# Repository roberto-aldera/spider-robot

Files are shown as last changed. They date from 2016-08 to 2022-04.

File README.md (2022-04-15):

# spider-robot 🕷️
⚠️ Messy research code 👨‍🎓

This repo contains the source code from my undergraduate mechatronics thesis project at the University of Cape Town.
An STM iNEMO was used for the data logging and control of a bio-inspired spider robot.
The majority of the development code is in C for use onboard the microcontroller, with some C# that was required for a logging app on my laptop.

📽️ Demo video available [here](https://youtu.be/Y-Pgbu4grWk).

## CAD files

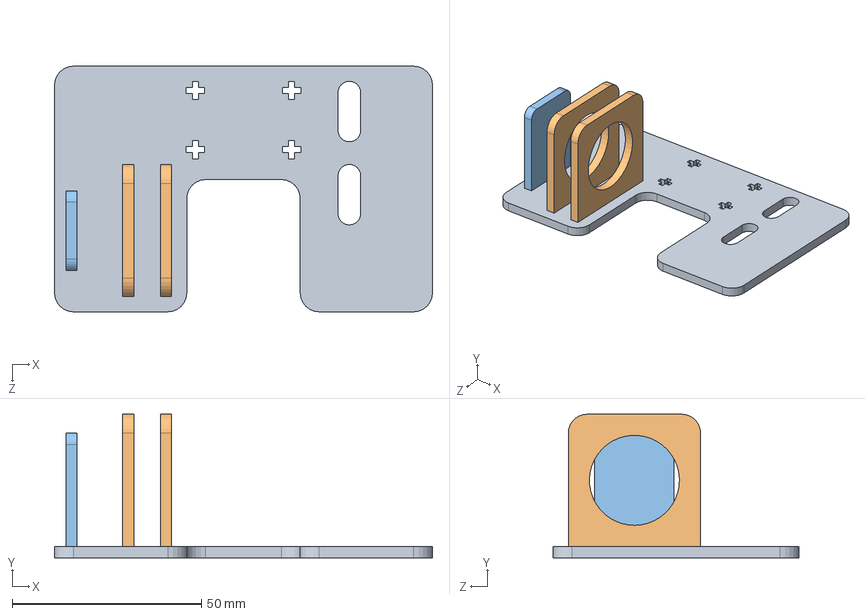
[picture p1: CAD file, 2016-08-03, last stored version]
SolidWorks parts/base_plate_assembly.SLDASM
100.0 x 38.0 x 65.0 mm
base_plate
dragline_motor_arch x 2
encoder_mount

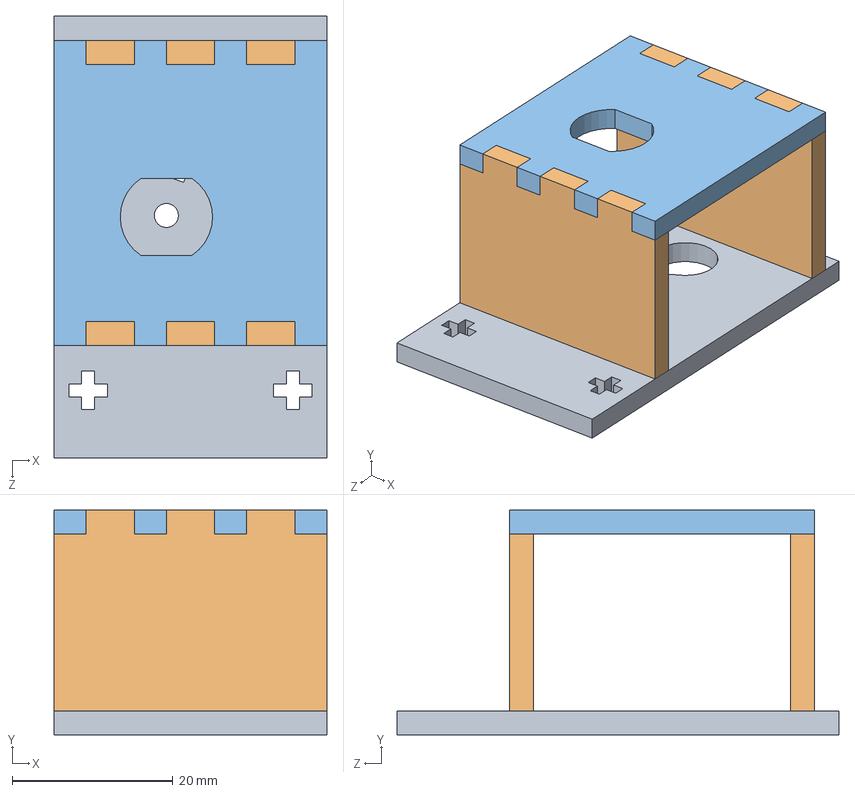
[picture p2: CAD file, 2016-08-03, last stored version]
SolidWorks parts/nail_launcher.SLDASM
34.0 x 28.0 x 55.0 mm
launcher_slot_new
launcher_motor_sides x 2
launcher_motor_holder

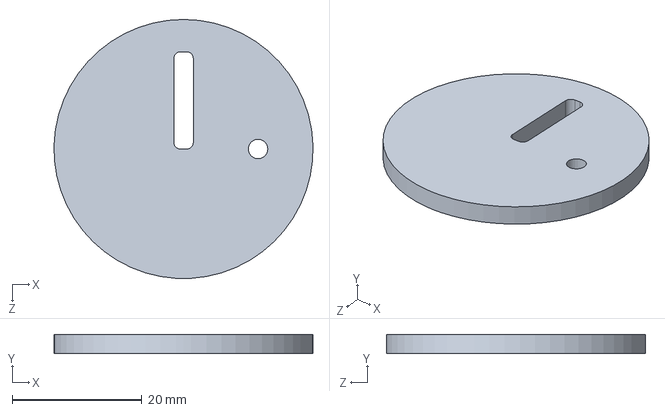
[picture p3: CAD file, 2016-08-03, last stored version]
SolidWorks parts/launcher_disc_slot.SLDPRT
40.0 x 3.00 x 40.0 mm

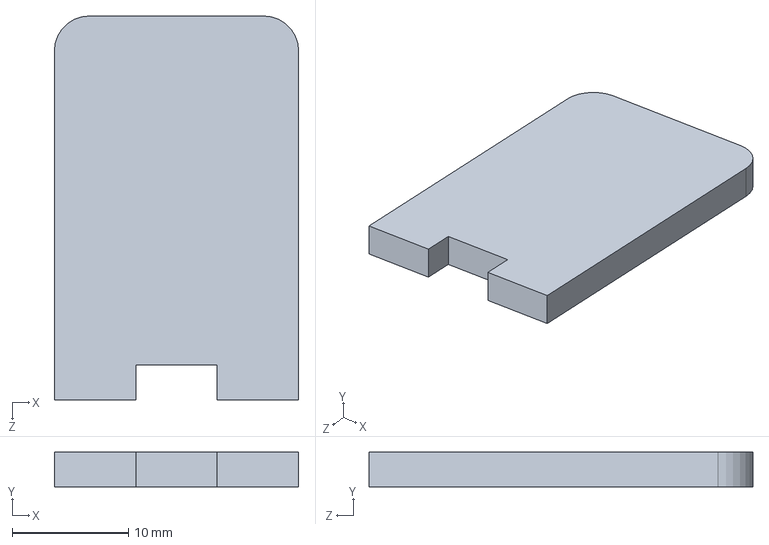
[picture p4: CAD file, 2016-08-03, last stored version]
SolidWorks parts/encoder_mount.SLDPRT
21.0 x 3.00 x 33.0 mm

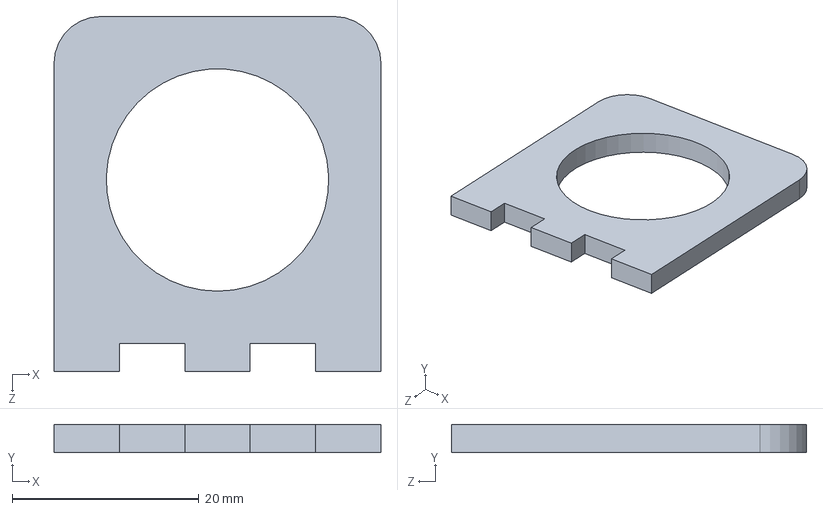
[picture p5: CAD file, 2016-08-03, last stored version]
SolidWorks parts/dragline_motor_arch.SLDPRT
35.0 x 3.00 x 38.0 mm

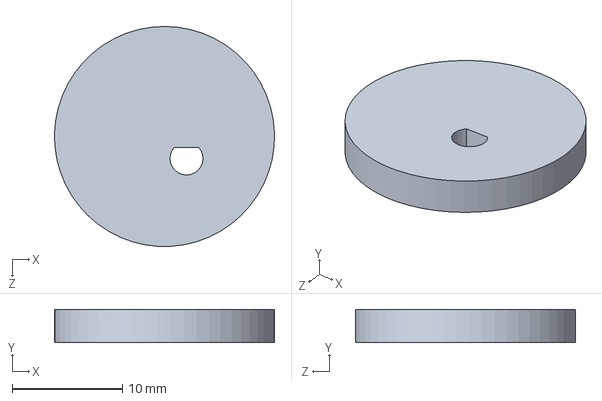
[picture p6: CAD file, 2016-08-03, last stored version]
SolidWorks parts/launcher_simple_cam.SLDPRT
20.0 x 3.00 x 20.0 mm

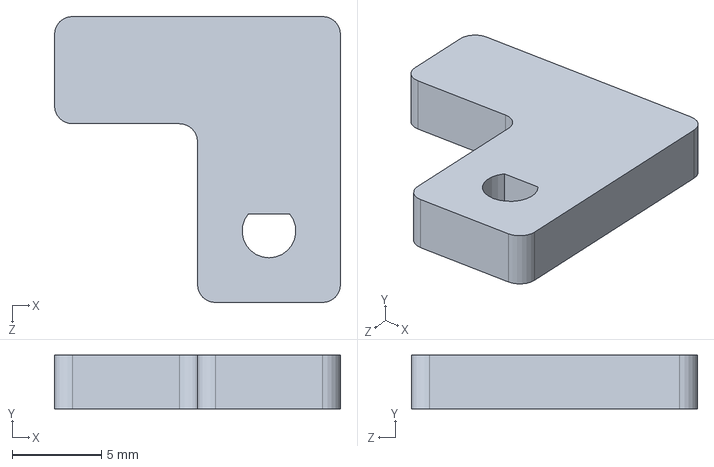
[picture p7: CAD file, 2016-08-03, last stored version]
SolidWorks parts/launcher_motor_L_arm.SLDPRT
16.0 x 3.00 x 16.0 mm

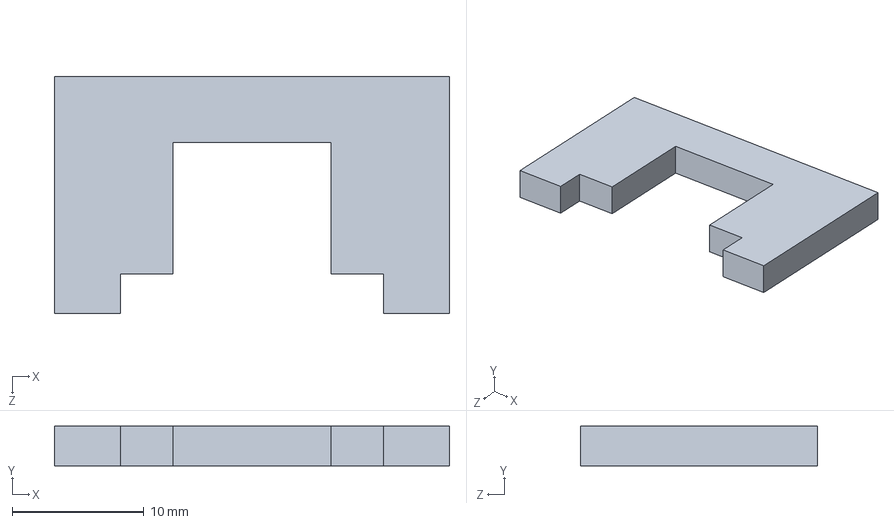
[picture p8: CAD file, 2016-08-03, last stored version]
SolidWorks parts/launcher_motor_arch.SLDPRT
30.0 x 3.00 x 18.0 mm

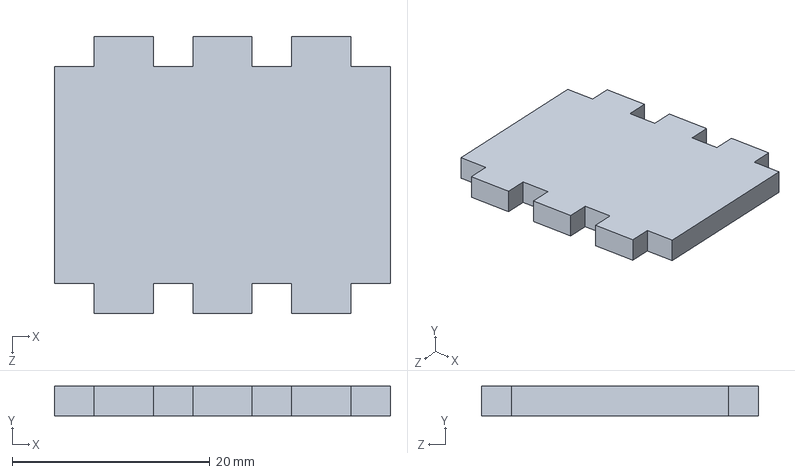
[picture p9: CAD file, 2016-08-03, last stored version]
SolidWorks parts/launcher_motor_sides.SLDPRT
34.0 x 3.00 x 28.0 mm

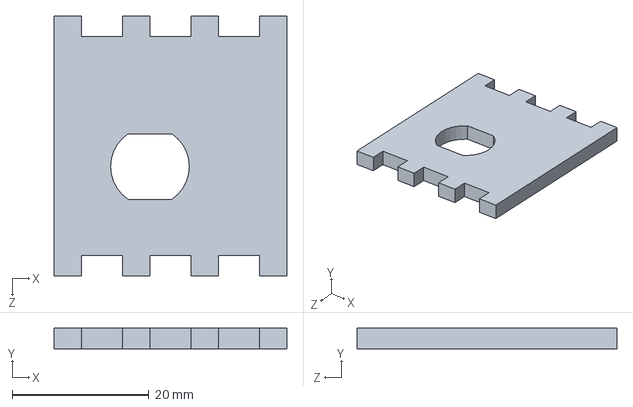
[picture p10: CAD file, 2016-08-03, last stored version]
SolidWorks parts/launcher_motor_holder.SLDPRT
34.0 x 3.00 x 38.0 mm

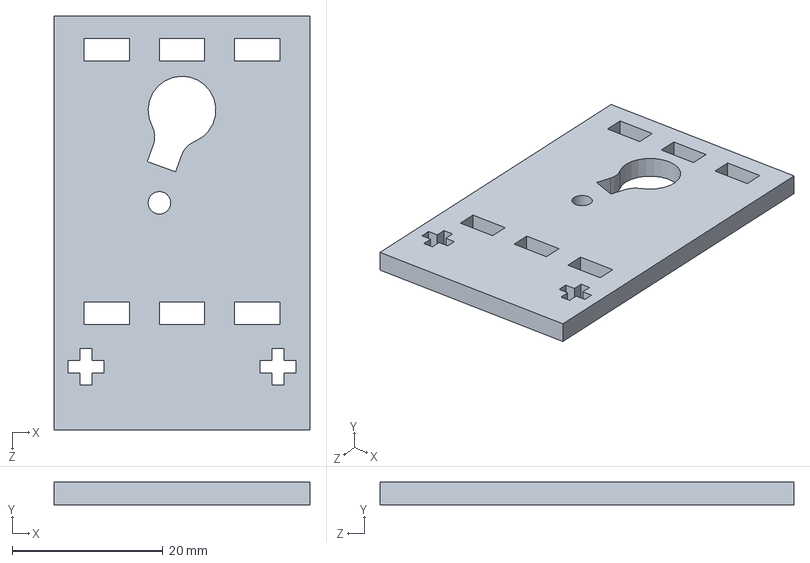
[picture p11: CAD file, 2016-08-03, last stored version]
SolidWorks parts/launcher_slot_new.SLDPRT
34.0 x 3.00 x 55.0 mm

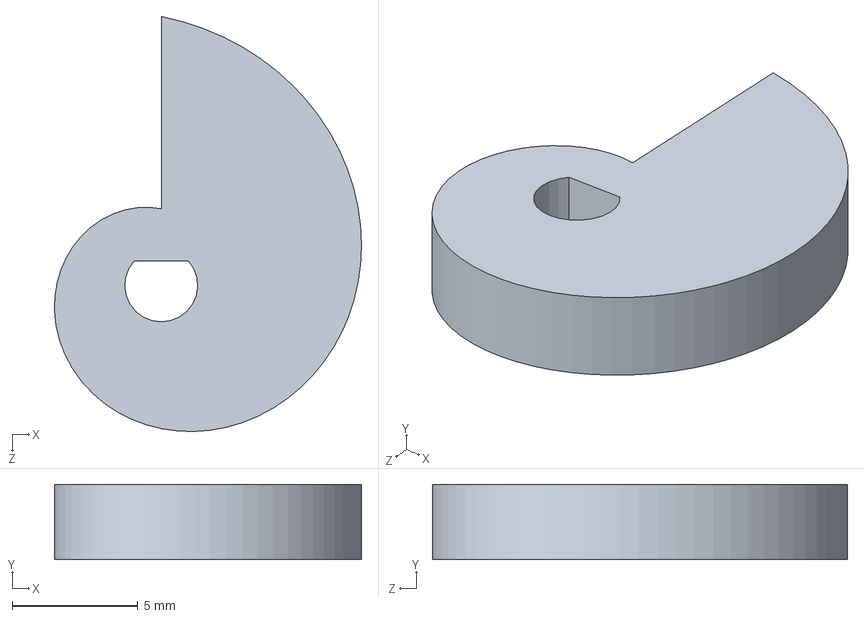
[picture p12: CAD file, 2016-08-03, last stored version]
SolidWorks parts/Nautilus_cam.SLDPRT
12.2 x 3.00 x 16.5 mm

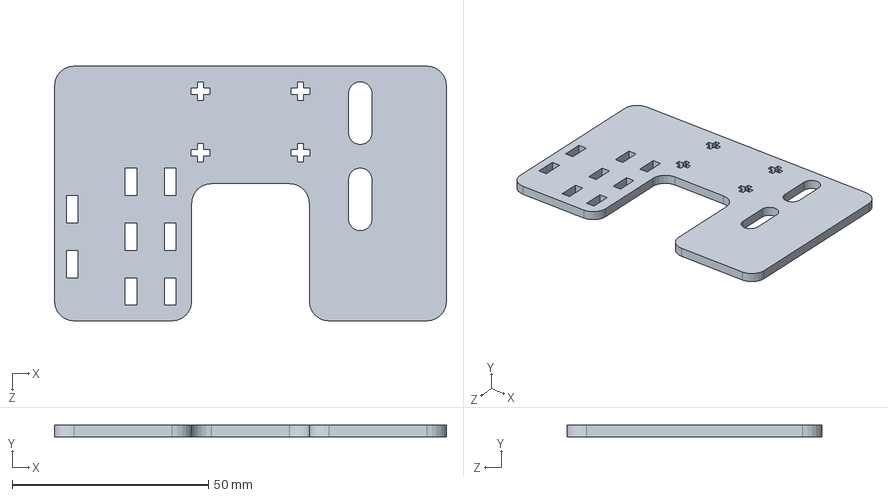
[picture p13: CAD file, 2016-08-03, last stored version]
SolidWorks parts/base_plate.SLDPRT
100.0 x 3.00 x 65.0 mm

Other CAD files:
SolidWorks parts/Nautilus_cams_sizing.SLDDRW
SolidWorks parts/base_plate_iterations.SLDDRW
SolidWorks parts/launcher_iterations.SLDDRW

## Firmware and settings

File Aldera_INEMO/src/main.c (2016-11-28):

/*
 * main.c
 *
 *  Created on: May 25, 2014
 *  Original author: Callen Fisher
 *  Current author: Roberto Aldera, Thesis 2016
 */
//Include all the relevant (header) files
//#include <stddef.h>
#include "stm32f10x.h"
#include "AccMag.h"
#include "controlLoopTimer.h"
#include "gpioPorts.h"
#include "gyro.h"
#include "testPorts.h"
#include "XBEE.h"
#include "USART.h"
#include "DMA.h"
#include "ADC.h"
#include "control.h"
#include "send.h"
#include "serial_terminal.h"
#include "CRC.h"
#include "pwm.h"

uint8_t acc8[6];		//3 axes, each returning uint16_t, 3x2=6
uint8_t mag8[6];
uint8_t gyro8[6];
uint8_t angles8[12];
uint8_t MiscPayload8[17];	//temperature=1 (just ADCtemp),PWM=4,Encoder=4+4, currentSensor=4
uint16_t encoderPosition = 0;
uint16_t adcValDMA[2];	//to store temperature and current sensor readings
uint16_t testVar[2];	//debugging purposes
uint8_t temperature[2];
uint8_t status = 0;
uint8_t XBee_waiting = 0;
uint8_t activateControl = 0;
float acc[3];
float accCalib[3];
float mag[3];
float gyro[3];
float gyroCalib[3];
float angles[3];
float velocities[3];
float positions[3];
float PWMval;
float shaft_revs = 0;
float shaft_speed = 0;
float motorCurrent;	//ADC reading from motor current sensor

void setUpEncoder();
void convertDataToBytes(void);
void toggleGPIOpin(uint8_t *status);

uint8_t a8[] = { 65, 66, 67, 68, 69, 70 };	//debugging
uint8_t b8[] = { 106, 107, 108, 109, 110, 111 };	//debugging
uint8_t c8[] = { 74, 75, 76, 77, 78, 79, 74, 75, 76, 77, 78, 79 };	//debugging
uint8_t d8[] = { 97, 98, 99, 100, 101, 102, 103, 102, 101, 100, 99, 98, 97 };//debugging

int main(void) {
	serialTerminal_Init();
	setUpLoopTimer();
	setUpEncoder();
	setUpGPIO();
	setUpEcompass();
	setUpGyro();
	setUpADC();	//this also sets up DMA...
	//setUpXbee(); //unused, replaced with SD card logging
	setUpLoggerSDcard();
	setUpPWM();

//	for(int i = 0; i < 999999; i++){
//	//ensure the data.txt file starts with the beginning of a packet
//	}

	while (1) {
		toggleGPIOpin(&status);
		getAcc(acc8, acc);		//this takes long
		getGyro(gyro8, gyro);
		//		getMag(mag8, mag);
		//		getTempCelsius(temperature);
		readADCdma(adcValDMA,&motorCurrent);	//for getting temperature, a u16 val
		//readADC_motorCurrent(&motorCurrent);	//for getting current, a float val
		temperature[1] = (uint8_t)((V25 - adcValDMA[0]) / Avg_Slope + 25);
		readEncoder(&shaft_revs, &shaft_speed);
		calibrateMEMS(acc, accCalib, gyro, gyroCalib, temperature);
		controlMethod(accCalib, gyroCalib, temperature, angles, velocities, positions,
				&PWMval, &shaft_revs, &activateControl);

		for (int p = 0; p < sizeof(TxBuff); p++) {
			TxBuff[p] = 0;
		}

		DMA_Cmd(DMA1_Channel7, DISABLE);
		DMA_SetCurrDataCounter(DMA1_Channel7, sizeof(TxBuff));
		DMA_Cmd(DMA1_Channel4, DISABLE);
		DMA_SetCurrDataCounter(DMA1_Channel4, sizeof(TxBuff));

		//Four payloads, gyro/acc/angles/MiscPayload
		convertDataToBytes();
		serialTerminal_packetize(gyro8, acc8, angles8, MiscPayload8,
				sizeof(gyro8), sizeof(acc8), sizeof(angles8),
				sizeof(MiscPayload8));

		//debugging purposes
		//		serialTerminal_packetize(a8, b8, c8, d8, sizeof(a8), sizeof(b8),
		//				sizeof(c8), sizeof(d8));

		//SD card data
		DMA_Cmd(DMA1_Channel4, ENABLE);
		USART_DMACmd(USART1, USART_DMAReq_Tx, ENABLE);
		USART_Cmd(USART1, ENABLE);

		//XBee data, slower
//		if (XBee_waiting == 10) {
//			DMA_Cmd(DMA1_Channel7, ENABLE);
//			USART_DMACmd(USART2, USART_DMAReq_Tx, ENABLE);
//			USART_Cmd(USART2, ENABLE);
//			XBee_waiting = 0;
//		}
//		XBee_waiting++;
		//Toggle PA11 to test loop frequency
		toggleGPIOpin(&status);
		//wait until next run, to maintain 200Hz sync
		waitForEndTimerHz();
	}
}

void toggleGPIOpin(uint8_t *status) {
	if (*status == 0) {
		GPIO_SetBits(GPIOA, GPIO_Pin_11);
		*status = 1;
	} else {
		GPIO_ResetBits(GPIOA, GPIO_Pin_11);
		*status = 0;
	}
}

void convertDataToBytes() {
	union {
		char temp_char[12];
		float temp_int_buffer[3];
	} buffer_to_char_union1;
	buffer_to_char_union1.temp_int_buffer[0] = angles[0];
	buffer_to_char_union1.temp_int_buffer[1] = angles[1];
	buffer_to_char_union1.temp_int_buffer[2] = angles[2];
	for (int i = 0; i < 12; i++) {
		angles8[i] = buffer_to_char_union1.temp_char[i];
	}

	//	union {
	//		uint8_t temp_signed[2];
	//		uint8_t temp_unsigned[2];
	//	} buffer_to_char_union2;
	//	//temperatureToPack[1] = 30;
	//	buffer_to_char_union2.temp_signed[0] = temperature[0];
	//	buffer_to_char_union2.temp_signed[1] = temperature[1];
	//	for (int i = 0; i < 2; i++) {
	//		MiscPayload8[i] = buffer_to_char_union2.temp_unsigned[i];
	//	}
	for (int i = 0; i < 1; i++) {
		//		MiscPayload8[i] = temperature[i];
		MiscPayload8[0] = temperature[1];
	}

	union {
		char temp_char[4];
		float temp_int_buffer;
	} buffer_to_char_union3;
	buffer_to_char_union3.temp_int_buffer = PWMval;
	for (int i = 1; i < 5; i++) {
		MiscPayload8[i] = buffer_to_char_union3.temp_char[i - 1];
	}

	union {
		char temp_char[4];
		float temp_int_buffer;
	} buffer_to_char_union4;
	buffer_to_char_union4.temp_int_buffer = shaft_revs;
	for (int i = 5; i < 9; i++) {
		MiscPayload8[i] = buffer_to_char_union4.temp_char[i - 5];
	}

	union {
		char temp_char[4];
		float temp_int_buffer;
	} buffer_to_char_union5;
	buffer_to_char_union5.temp_int_buffer = shaft_speed;
	for (int i = 9; i < 13; i++) {
		MiscPayload8[i] = buffer_to_char_union5.temp_char[i - 9];
	}

	union {
		char temp_char[4];
		float temp_int_buffer;
	} buffer_to_char_union6;
	buffer_to_char_union6.temp_int_buffer = motorCurrent;
	for (int i = 13; i < 17; i++) {
		MiscPayload8[i] = buffer_to_char_union6.temp_char[i - 13];
	}
}

///////////////////////////////////////////////////////////////////////////
/////don't delete the following functions//////////////////////////////////
///////////////////////////////////////////////////////////////////////////
void __assert_func(const char *file, int line, const char *func,
		const char *failedexpr) {
	while (1) {
	}
}
void __assert(const char *file, int line, const char *failedexpr) {
	__assert_func(file, line, NULL, failedexpr);
}

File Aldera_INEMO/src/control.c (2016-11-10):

/*
 * control.c
 *
 *  Created on: Jun 9, 2014
 *  Template: Callen Fisher
 *  Author: Roberto Aldera
 *
 */

#include "control.h"

void readEncoder(float *shaft_revs, float *shaft_speed) {

	static volatile int16_t oldShaftEncoder;
	static volatile int16_t shaftEncoder;
	static float position = 0;

	oldShaftEncoder = shaftEncoder;
	shaftEncoder = TIM_GetCounter(TIM3);
	*shaft_speed = shaftEncoder - oldShaftEncoder;
	position += *shaft_speed;
	*shaft_revs = position;
	//	if (shaftEncoder > 32768) {
	//		shaftEncoder = -(65536 - shaftEncoder);
	//	}
	//	*shaft_revs = (position) ;//(1/(3*2));	//3 teeth on encoder wheel
	//*shaft_speed = *shaft_speed / 0.01;

}

void calibrateMEMS(float* acc, float* accCalib, float* gyro, float* gyroCalib, u8* temperature){
	accCalib[0] = 0.9922*acc[0] - 0.0247*acc[1] + 0.0225*acc[2] + 0.0468;
	accCalib[1] = 0.0453*acc[0] + 0.9574*acc[1] + 0.0072*acc[2] + 0.022;
	accCalib[2] = -0.0141*acc[0] -0.0037*acc[1] + 0.9971*acc[2] + 0.0053;

	gyroCalib[0] = gyro[0] + (0.060394*temperature[1] - 3.0843);
	gyroCalib[1] = gyro[1] + (0.025522*temperature[1] - 0.40084);
	gyroCalib[2] = gyro[2] + (-0.32248*temperature[1] + 11.3496);
}

void controlMethod(float*accCalib, float*gyroCalib, uint8_t*temp, float*angles, float*velocities,
		float*positions,float*PWMval,float*shaft_revs,uint8_t*activateControl) //perform all control in this method
{
	//3 floats sent in angles (12 bytes total)
	angles[0] = angles[0] + gyroCalib[0]*0.01;
	angles[1] = angles[1] + gyroCalib[1]*0.01;
	angles[2] = angles[2] + gyroCalib[2]*0.01;

	//Velocities from acc data
	velocities[0] = velocities[0] + 9.81*accCalib[0]*0.01;
	velocities[1] = velocities[1] + 9.81*accCalib[1]*0.01;
	velocities[2] = velocities[2] + 9.81*accCalib[2]*0.01;

	//Positions from velocity from acc data
	positions[0] = positions[0] + velocities[0]*0.01;
	positions[1] = positions[1] + velocities[1]*0.01;
	positions[2] = positions[2] + velocities[2]*0.01;

	//do PFL
/*	if ((*shaft_revs != 0)){// && (*activateControl == 1)){
		float mass = 0.226;		//robot mass
		float radius = 0.01;	//spool radius
		float Kphi = 0.0227;	//motor constant
		float Length_dragline = 0.0037*(*shaft_revs);	//dragline ratio to SI units
		float thS = asin(positions[2]/Length_dragline);
		float i_cmd = (mass*radius/Kphi)*(-0.1*velocities[0]/cos(thS));
		//float i_cmd = 0.5;
		*PWMval = (i_cmd+0.05)/0.00465;

	}*/
	//turn off motor PWM control after 0.5 s

	//to wind up dragline manually after jumping
	if (GPIO_ReadInputDataBit(GPIOA, GPIO_Pin_9) != 0) {
		//*activateControl = 1;
		*PWMval = *PWMval+0.2;	//was 20
		setPWM(PWMval);
	} else {
		*PWMval = 0;
		setPWM(PWMval);

		//*PWMval = *PWMval+0.2;	//was 20
		/*while (*activateControl == 0){
			*PWMval = 0;	//was 20
			setPWM(PWMval);
			*activateControl = 1;
		}*/

	}

}

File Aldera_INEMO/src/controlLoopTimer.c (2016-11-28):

/*
 * controlLoopTimer.c
 *
 *  Created on: Jun 6, 2014
 *      Author: Callen Fisher
 */

#include "controlLoopTimer.h"

int proceed10ms = 0;
///////////////////////////////////////////////////////////////////////////
////////////////main loop timer ///////////////////////////////////////////
///////////////////////////////////////////////////////////////////////////
void setUpLoopTimer(void) {
	RCC_APB1PeriphClockCmd(RCC_APB1Periph_TIM2, ENABLE);

	NVIC_InitTypeDef NVIC_InitStructure;
	/* Enable the TIM2 global Interrupt */
	NVIC_InitStructure.NVIC_IRQChannel = TIM2_IRQn; //set up the interrupt handler for TIM2
	NVIC_InitStructure.NVIC_IRQChannelPreemptionPriority = 0;
	NVIC_InitStructure.NVIC_IRQChannelSubPriority = 1;
	NVIC_InitStructure.NVIC_IRQChannelCmd = ENABLE;

	NVIC_Init(&NVIC_InitStructure);

	TIM_TimeBaseInitTypeDef TIM_TimeBaseStruct;

	TIM_TimeBaseStruct.TIM_ClockDivision = TIM_CKD_DIV1;
	TIM_TimeBaseStruct.TIM_CounterMode = TIM_CounterMode_Up;
	//TIM_TimeBaseStruct.TIM_Period = (7200 / 4 - 1); //makes it 100Hz - confirmed on scope.
	TIM_TimeBaseStruct.TIM_Period = (3600 / 4 - 1); //experimenting, 200Hz
	//TIM_TimeBaseStruct.TIM_Period = (2888 / 4 - 1); //experimenting, 250Hz
	//TIM_TimeBaseStruct.TIM_Period = (1440 / 4 - 1); //experimenting, 500Hz
	TIM_TimeBaseStruct.TIM_Prescaler = 400 - 1;
	TIM_TimeBaseStruct.TIM_RepetitionCounter = 0x0000;

	TIM_TimeBaseInit(TIM2, &TIM_TimeBaseStruct);

	TIM_Cmd(TIM2, ENABLE);

	TIM_ITConfig(TIM2, TIM_IT_Update, ENABLE);

}

void TIM2_IRQHandler(void) {
	if (TIM_GetITStatus(TIM2, TIM_IT_Update) != RESET) {
		TIM_ClearITPendingBit(TIM2, TIM_IT_Update);

		proceed10ms = 1;
	}
}

void setUpEncoder(void) {
//http://www.micromouseonline.com/2013/02/16/quadrature-encoders-with-the-stm32f4/
//https://my.st.com/public/STe2ecommunities/mcu/Lists/cortex_mx_stm32/Flat.aspx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
	RCC_APB1PeriphClockCmd(RCC_APB1Periph_TIM3, ENABLE);
	TIM_TimeBaseInitTypeDef TIM_TimeBaseStructure;
	TIM_TimeBaseStructure.TIM_Prescaler = 0;
	TIM_TimeBaseStructure.TIM_Period = 65535; // Maximal
	TIM_TimeBaseStructure.TIM_ClockDivision = TIM_CKD_DIV1;
	TIM_TimeBaseStructure.TIM_CounterMode = TIM_CounterMode_Up;

	TIM_TimeBaseInit(TIM3, &TIM_TimeBaseStructure);

	// TIM_EncoderMode_TI1: Counter counts on TI1FP1 edge depending on TI2FP2 level.
	TIM_EncoderInterfaceConfig(TIM3, TIM_EncoderMode_TI1, TIM_ICPolarity_Rising,
			TIM_ICPolarity_Rising);

	TIM_Cmd(TIM3, ENABLE);
}

void waitForEndTimerHz(void) {
	while (proceed10ms == 0) //interrupt will set proceed to 1;
	{

	}
	proceed10ms = 0;
}

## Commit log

2016-07-26 Bulk upload of other files
    [Nautilus_cam.SLDPRT, Nautilus_cams_sizing.SLDDRW]
2016-07-26 More bulk uploading
    [INEMOundergrad.SchDoc, INEMOundergradPCB.PcbDoc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]
2016-08-03 Bulk upload before beginning code
    [Nautilus_cam.SLDPRT, base_plate.SLDPRT, base_plate_assembly.SLDASM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]
2016-08-04 Loop running at 100Hz, and added encoder datasheets
2016-08-04 Removing non-INEMO files
    [INEMOundergrad.SchDoc, INEMOundergradPCB.PcbDoc, Nautilus_cam.SLDPRT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]
2016-08-12 Read data into app, still working on reading in temperature
2016-08-13 Add temperature to packet and send to app (not yet correct values though)
    [main.c]
2016-08-16 Add pushbutton to toggle PWM to H-Bridge, move PWM from PA6 to PA10 to allow for all signals on one Molex connector
2016-08-17 Take DMA out of circular mode (put it in normal mode)
2016-08-17 Fix control loop frequency to be 100Hz, was actually running at 200Hz which was too fast for Xbee comms
    [controlLoopTimer.c]
2016-08-17 Remove hacky delay, no longer necessary now that DMA and control loop are set up correctly. getTemp is causing a hard fault, fix later.
    [main.c]
2016-08-17 Correct Acc and Gyro values to true values, beware of byte order for the Gyro (MSB/LSB)
    [AccMag.c, gyro.c]
2016-08-20 Add encoder reading in Atollic, but still need to get packet sending successfully with encoder data to the app
2016-08-21 Add encoder reading into the app, removed temperature to make space (packet size was too large and causing issues, must be fixed later). CRC errors in app are now appearing.
    [control.c, main.c]
2016-08-24 Add ADC temperature reading, Accelerometer values are off now and need fixing
    [ADC.c, control.c, gyro.c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]
2016-08-24 Move 100Hz loop code into interrupt, but still having trouble getting the app to pick up data without adding in a delay in the main loop
2016-08-25 Remove 100Hz loop, clean up a bit, about to begin input cpature for encoder reading in
2016-08-25 InputCapture for encoder position, cleaning up code
2016-08-25 Include placeholder for shaft speed in packet, increase buffer size, feed data into app successfully.
2016-08-26 Add encoder speed, still not working properly yet
    [control.c, controlLoopTimer.c, main.c]
2016-09-02 Add some encoder code, commented out a lot of other code, distance/speed is sort of working
2016-09-12 Read encoder position using TIM3, clean up old code, encoder speed is questionable...
2016-09-12 Change encoder speed/position to read in teeth counts, speed still questionable.
2016-09-25 Update app every frame, add information to GUI regarding data and control loop frequencies (20Hz, 100Hz)
2016-09-26 Add motor current value from ADC to GUI
2016-09-26 Reading ADC for both temperature and current sensor on PA5, still needs to be cleaned up a lot
2016-10-03 Read current and temperature on two ADCs, map current value to mA
2016-10-18 Change motor current from mA to amps (uint16 now a float). Code needs some serious cleaning up.
2016-11-01 Add calibration code for gyro and acc sensors, and set angle floats to meaningful values.
2016-11-01 Adding velocity and position data from acc sensor data.
2016-11-08 Increase buffer size and add delay to improve log reliability. Change gyro resolution to 2000dps.
2016-11-25 First post-handin edits, run control loop at 200Hz.
2016-11-25 Remove Xbee setup code, still 200Hz, and reduce motorCurrent reading inefficiencies
2016-11-28 Up I2C speed from 100kHz to 400kHz to reduce delay in getting Acc data
2016-11-28 Change loop timer to 200Hz, logging successfully to SD card without corruption
